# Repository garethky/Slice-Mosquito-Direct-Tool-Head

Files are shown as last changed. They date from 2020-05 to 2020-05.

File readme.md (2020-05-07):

# About

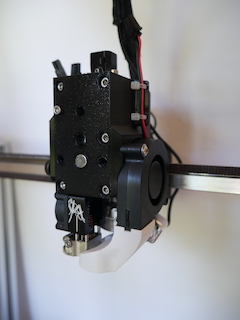
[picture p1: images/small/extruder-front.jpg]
Extruder Front

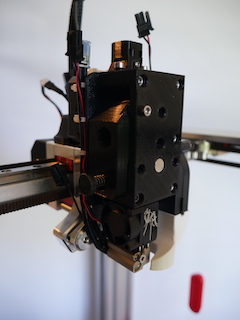
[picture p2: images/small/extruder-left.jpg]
Extruder Left


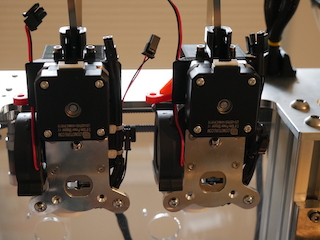
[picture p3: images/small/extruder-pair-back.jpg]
Extruder Pair Back

<a href="https://raw.githubusercontent.com/garethky/Slice-Mosquito-Direct-Tool-Head/master/images/extruder-pair-left.jpg">Extruder Pair Side</a>

This is a tool designed for the E3D Tool Changer platform. It uses the Bondtech Mini Gear (BMG) drive parts and the Slice Engineering Mosquito for a compact and light weight direct drive extruder.

# Source

The project was designed in OnShape and you can access the released design here: [E3D Tool Changer - Bondtech Mini Gear (BMG)/Slice Mosquito Tool Head](https://cad.onshape.com/documents/296b560eee7721bd4ef989d0/w/90142d42ff99dde68f53c17c/e/d21c095bd78c720c7f814c17). 

The project is configured to allow forking and export of .stl and other formats. Work may be in progress, for the latest tested .stl files please use this github repo.

STL files, this readme and these assembly instructions are maintained on [GitHub - Slice-Mosquito-Direct-Tool-Head](https://github.com/garethky/Slice-Mosquito-Direct-Tool-Head), you can also file an issue there.

## Why Build One?
* It's a geared direct drive extruder that can print faster and more precisely that the stock bowden tooling.
* The Mosquito hot end makes it very easy to swap nozzles without worrying about filament oozing out of your hot end. "Volcano" version of the Mosquito has the same nozzle hight so they can share wipers/brushes.
* It uses the stock dock pins in its stock location. No dock mods required.
* Light weight. Measured as 400g all up weight with tool plate.
* 5015 part cooling for quiet and powerful cooling.
* Compact size, wont steal space from other tools or collide with the printer frame.
* Designed for manufacture on FDM printers with no required support material in PETG filament.

## Project Status: Beta
Currently this project is in Beta. Now is a good time to print an extruder and try it out for yourself. Before this release, several prototypes were printed and tested to failure. Improvements to the design have been made that should overcome these issues. Numerous print-ability tweaks have been made to eliminate the need for support material when printing. Print-ability, usability and general fit/finish should be fine for general use. I'm installing printing 4 on my tool changer so I can work on multi-material and multi-color printing.

## Required Parts, Printing & Assembly
[Assembly Instructions](assembly-instructions.md)

## Extruder Setup and Printing
[Extruder Setup & Printing](setup.md)

# Related Work
This design contains modification of 2 parts provided by E3D: 

* [X-Carriage Cable Bracket](https://github.com/e3donline/ToolChanger/blob/master/STLs/X-Carriage%20Cable%20Bracket.stl)
* [V6 Cable Support](https://github.com/e3donline/ToolChanger/blob/master/V6%20Tool/STLs/V6%20Cable%20Support.stl)

The modifications are just to move the bolt holes to re-position the parts. The source for the changes is available in OnShape. Later versions will aim to remove these parts as they are not central to the design and really not ideal, but they work well enough for now. Thank you E3D for making the designs available under the GPL.

# Q and A

### Is this done, will there be changes?

Oh there are going to be changes... when I get time:
1. Prusa Labs has released their filament sensor as open source and inexpensive third party kits are available. This will enable automated filament loading and unloading and filament runout detection. The next major release will have the filament sensor integrated as an optional add-on.
2. I'm not satisfied with the way the filament enters the extruder. This release eliminated the push fit connector I was using. Bondtech's connector is inexpensive and is being evaluated. for now simply using no connector is fine and makes filament swaps easier.
3. The Cable Support that attaches the metal band and wiring loom is something I want improve and possible integrate into the motor plate. The extra part and fasteners dont seem to be beneficial. Cable routing in general isnt as clean as I wanted.

### Will you adapt this design for the E3D V6?

The V6 mounts differently and the extruder would have to be split along the filament path to capture the mount. Thats a very big change and it wont be easy to maintain both versions. There is also the [Hemera](https://e3d-online.com/e3d-hemera-175-kit) which is a great value vs this design. You're free to fork the design if you like.

### How about Duet 3 Tool Board support?

I like the concept but the boards are kind of large. My worry with this is mostly about hwere to put it without making the whole package larger.

### That Mosquito fan is a menace

I noticed that too. Slice recommends running their fan at 70% (per https://www.sliceengineering.com/pages/documentation). Only the main Duet 2 board has PWM controlled ports for the hot end coolers to permit this. The Duet 3 expansion board has PWM fan ports. I'm upgrading to the Duet 3 and I'll be evaluating the noise at the 70% setting with 4 extruders. If thats too noisy, a mod to run a quieter fan would be something to consider. To have any benefit we would have to go up to the 40mm Noctua fan.

### Will you post this to Thingiverse/Prusa Printers/Other Platform

For the time being no. The audiance for this pretty narrow right now and for my workflow github is just nicer.

# Happy Printing!

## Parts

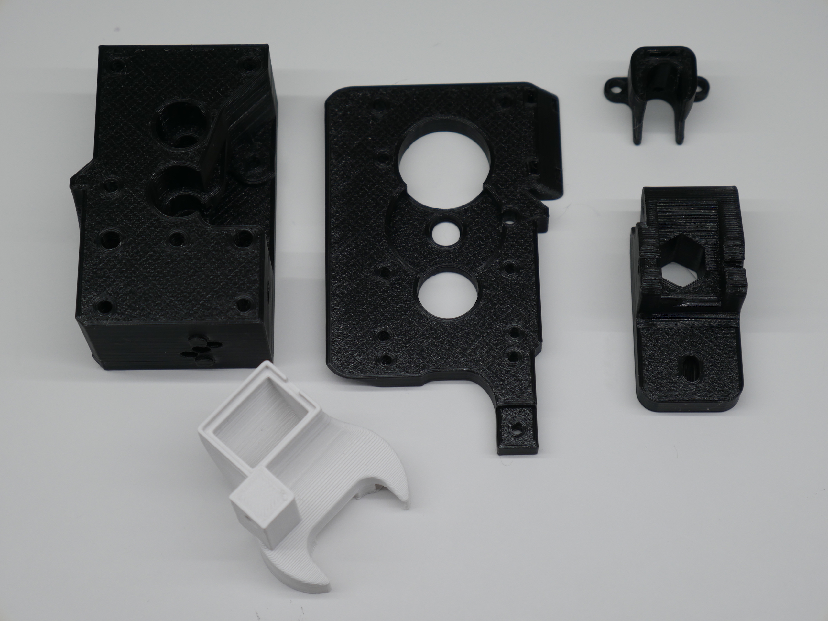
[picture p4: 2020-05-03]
images/assembly/printed-parts.jpg

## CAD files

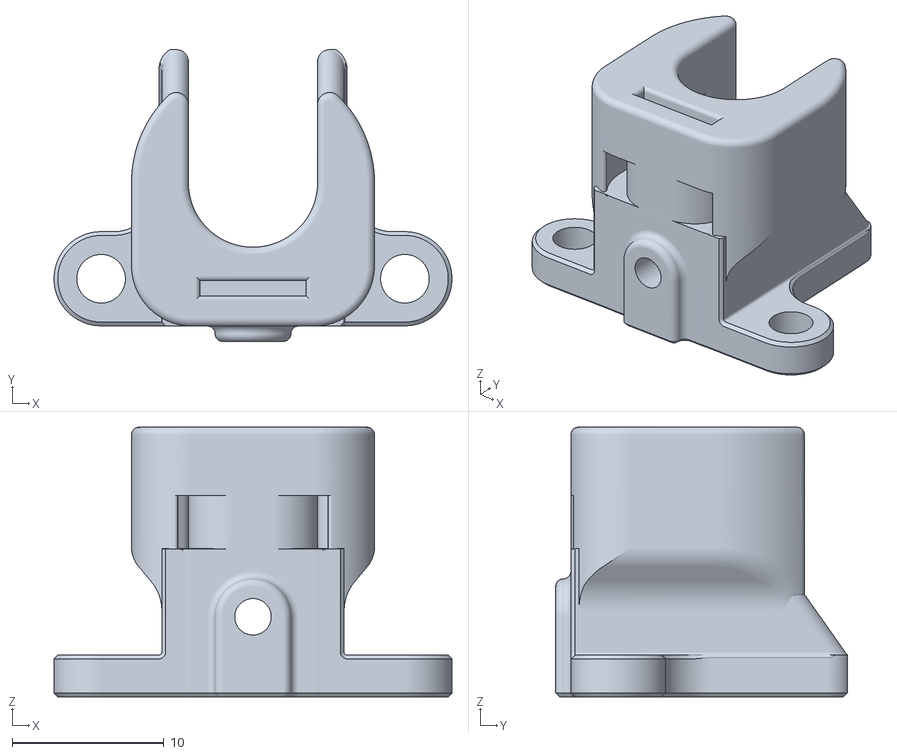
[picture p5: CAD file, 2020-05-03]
STL/Cable Support.stl
26.2 x 19.2 x 17.8

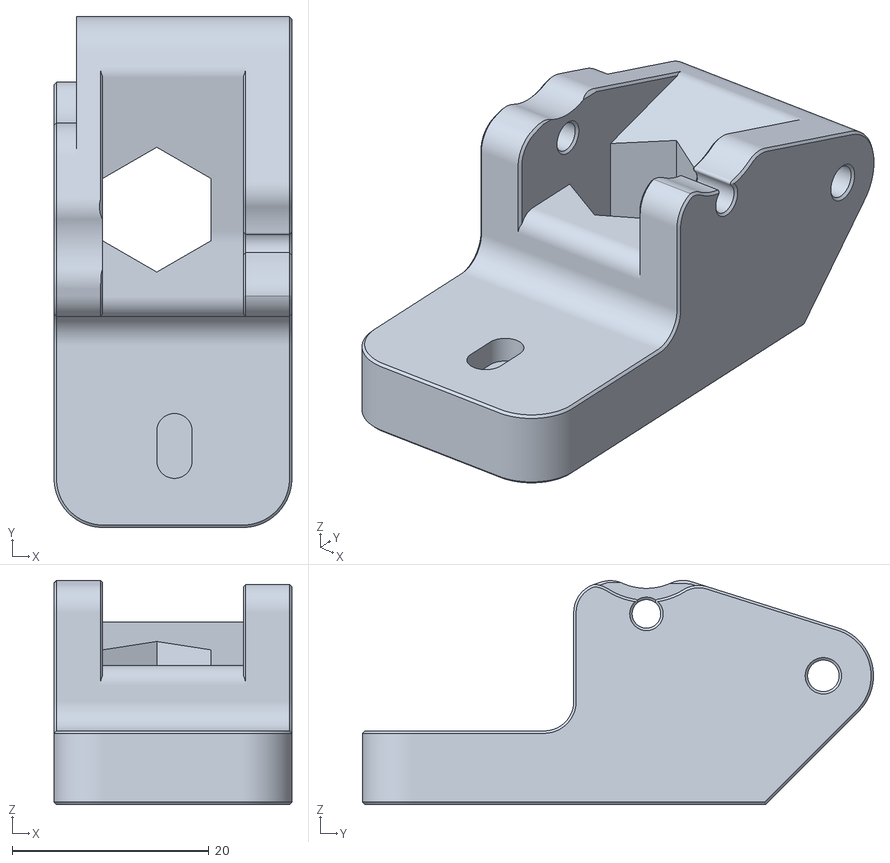
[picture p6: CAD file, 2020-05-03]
STL/Idler.stl
24.2 x 52.0 x 22.8

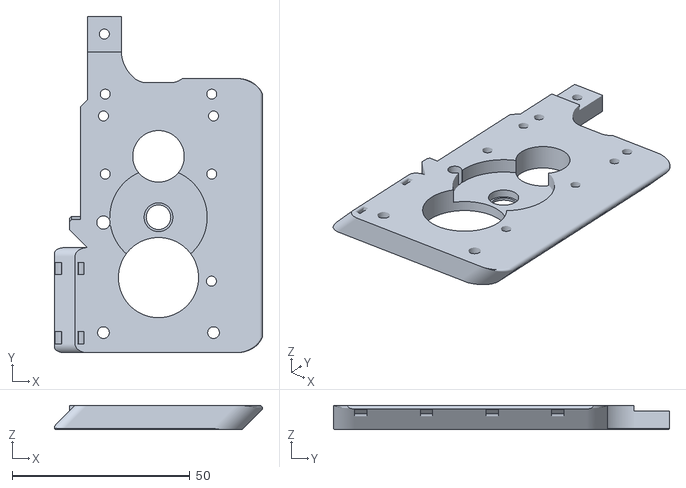
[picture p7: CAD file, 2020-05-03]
STL/Motor Plate.stl
58.6 x 94.7 x 6.79

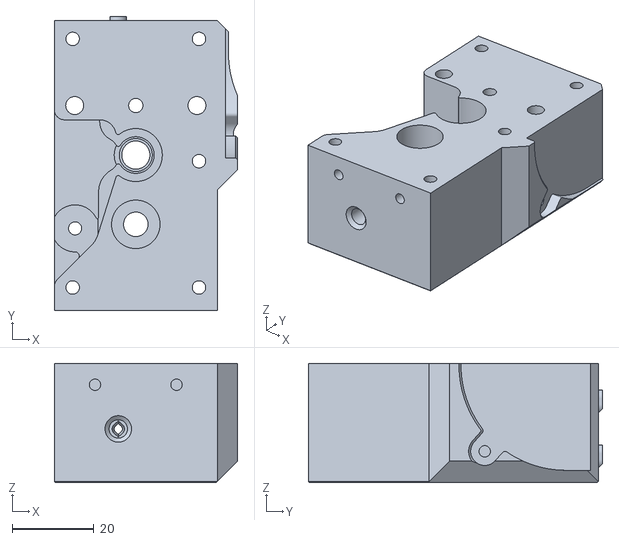
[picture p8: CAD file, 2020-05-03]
STL/Hot End Block.stl
45.0 x 72.1 x 29.2

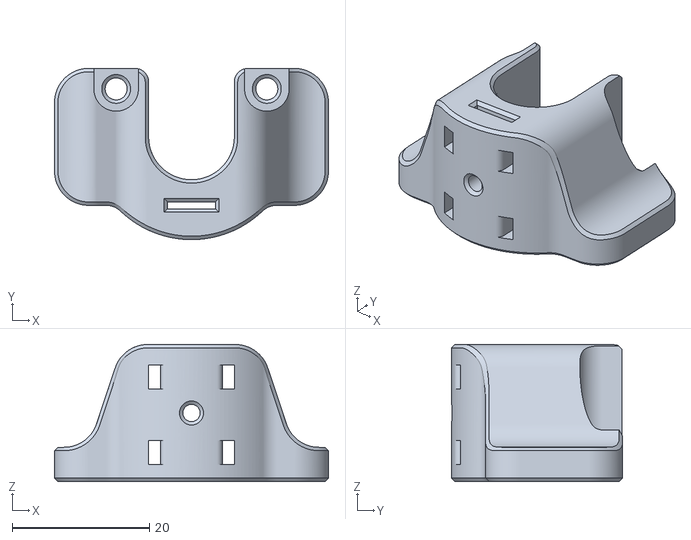
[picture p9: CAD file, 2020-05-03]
STL/X-Carriage Cable Bracket.stl
40.0 x 25.0 x 20.0

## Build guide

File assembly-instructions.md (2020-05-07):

## Hardware Required

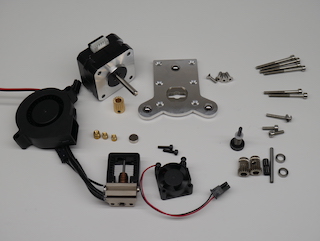
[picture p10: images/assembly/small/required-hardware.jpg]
all required hardware


* [Slice Mosquito Hot End](https://www.sliceengineering.com/collections/mosquito-the-professional-hotend). It does come with all the 2.5mm screws you will need to mount it. Note that the [cooling fan](https://www.sliceengineering.com/collections/accessories/products/fan-for-mosquito-hotend%E2%84%A2), [thermistor](https://www.sliceengineering.com/collections/accessories/products/thermistor-high-temperature) and [heater cartridge](https://www.sliceengineering.com/collections/accessories/products/50w-heater-cartridge) are not included and need to be purchased separately. E3D header cartridges and thermistors will work but the fan is particularly difficult to source so make sure your get that.
* Bondtech BMG Parts. They can be ordered as 'Spare Parts' directly from Bondtech (or from one of their local distributors like Filastruder) and wont cost as much as an entire BMG extruder:
    * 1 x [Bondtech Gear Kit 1.75/5.0](https://www.bondtech.se/en/product/drivegear-kits/) thats for 1.75mm filament and M5 shafts. The idler shaft included in the kit will no be used.
    * 1 x [Motor Gear](https://www.bondtech.se/en/product/motor-gear/)
    * 1 x [Reduction Shaft Assembly](https://www.bondtech.se/en/product/shaft-assembly/)
    * 1 x [3.0 x 32mm Shaft](https://www.bondtech.se/en/product/shafts/) You will need to cut this down to 24mm to be used as the idler shaft. This is the same size that Prusa use in their MK3 idler design. It's not a standard Bondtech part.
    * 2 x [5mm x 8mm x 2.5mm Bearings](https://www.bondtech.se/en/product/ballbearing-5x8x2-5/)
    * 1 x [Thumb Screw Assembly](https://www.bondtech.se/en/product-category/spare-parts/bondtech-spare-parts/thumbscrew-assembly/)
* A NEMA 17 stepper, preferably a "pancake" 25mm stepper, such as the [LDO-42STH25-1404MAC](https://www.bondtech.se/en/product/nema-17-motor-slim-power-ldo-42sth25-1404mac-0-9-degree/)
* Hardware 
    * M3 socket head cap screws:
        * 4 x 35mm
        * 2 x 30mm
        * 1 x 20mm with washer (a button head would also work)
        * 1 x 15mm
        * 2 x 10mm
    * 4 x M3 x 10mm Flat Head Cap Screws
    * 1 x M3 x 5mm set screw
    * Melt in Brass inserts for plastics
        * 2 x M2.5 x 5.5mm brass inserts, such as these: https://www.amazon.com/dp/B07NBPGTY2
        * 1 x M3 x 4mm brass threaded insert, such as these: https://www.amazon.com/dp/B077CJV3Z9
        * Note: dont cheap out on these parts as they are safety critical, [see testing by CNC Kitchen](https://www.youtube.com/watch?v=G-UF4tv3Hvc).
* Short length of PTFE tubing (~30mm)
* 8mm x 3mm Magnet (This size is [not uncommon](https://www.amazon.com/s?k=8mm+x+3mm+neodymium+magnets))
* 7+ small zip ties
* E3D ToolChanger [Tool Plate](https://e3d-online.com/toolchanger-blank-plate)
* A 5015 24V cooling fan such as [this one](https://www.amazon.com/dp/B07WFKPLWY).

## Printing The Parts

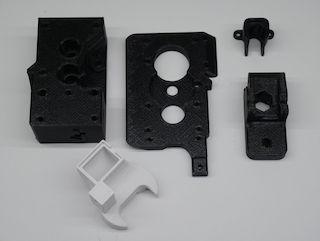
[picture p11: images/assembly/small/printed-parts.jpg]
all printed extruder parts


Every part has a face that was designed to print down on the print bed to help eliminate the need for supports. The SLT files should correctly orient the parts in your slicer when imported.

The extruder parts were designed to be printed in PETG. But the Fan Nozzle should only be printed in ASA, ABS or another hight temp filament.

I suggest using these settings for the extruder parts:
* 0.4mm nozzle
* 0.2mm layer height
* 3 perimeters (hot melt inserts need some material to melt into)
* 20% Gyroid or Grid infill

# Assembly
## Prepare the Stepper Motor

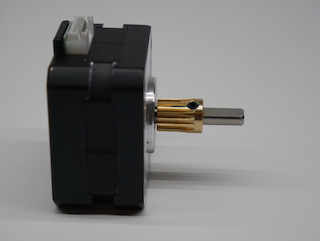
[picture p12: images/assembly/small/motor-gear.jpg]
motor gear


1. Install the drive gear on the stepper shaft so the toothed end faces the stepper and just clears the face of the stepper.

## Mosquito Preparation

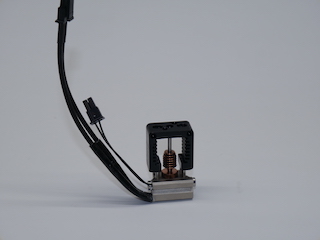
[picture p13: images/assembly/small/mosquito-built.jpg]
fully built mosquito


1. Install the heater and thermistor in the orientation shown. Follow Slice Engineerings instructions for doing this.

## Prepare the Hot End Block

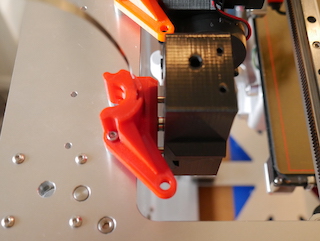
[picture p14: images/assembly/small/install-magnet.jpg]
install magnet


1. Install the magnet in the Hot End Block. It should be a press fit. Verify the magnet polarity with the Dock before installing. Use some thin CA glue to lock the magnet in permanently if desired. There is a hole in in the block that allows the magnet to be pushed out if polarity is wrong and for glue to get in.

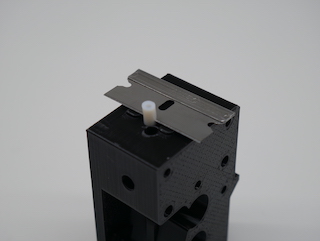
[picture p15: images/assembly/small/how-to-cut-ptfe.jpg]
how to cut ptfe


2. The extruder uses a very short length of PTFE tube to guide the filament into the Mosquito. The PTFE needs to be cut for length such that it fits into the 1mm deep pocket on top of the Mosquito, here is how to do that easily without measuring:
	1. Start with a longer length of PTFE tube thats easier to handle (30+mm).
	1. Cut one end square.
	1. Fully insert the square end of the PTFE tube into the bottom of the Hot End Block untill it stops (about 20mm).
	1. Cut the PTFE to final length by lining up a razor blade with the two locating bumps on the Hot End Block and cutting through the PTFE. The bumps stick out 1mm and act as a guide.

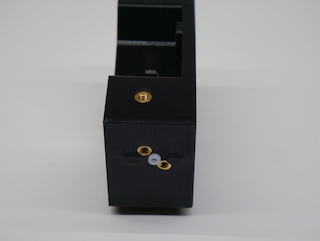
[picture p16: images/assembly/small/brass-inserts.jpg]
brass inserts installed


3. With the PTFE tube in place (this helps to prevent the thin walls from melting!), install the M2.5 brass threaded inserts for the Mosquito.
4. Install the M3 threaded insert for the Idler tension knob.

## Prepare the Idler

1. Cut away the printing support material in the tension knob hole/slot area with an exacto knife.
1. Place the Bontech idler gear with its two needle bearings into its final location in the idler. The hobbed section of the gear goes in front of the viewing window.

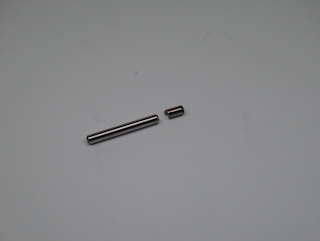
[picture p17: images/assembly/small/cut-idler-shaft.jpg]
cut idler shaft with cut off


3. Cut the 32mm x 3mm shaft down to 24mm.

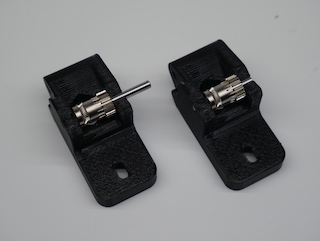
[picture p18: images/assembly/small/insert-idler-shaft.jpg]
insert idler shaft carefully


4. Insert the 24mm x 3mm shaft through the assembly so that it does not protrude from either side of the Idler. Reasonable force is required as these parts are an interference/pretensioned fit. The idler gear should now spin freely and have a tiny amount of play left to right. 

## Assemble the Drive Line

1. Install the bearings in the Motor Plate and Hot End Block. A pencil or pen is a good tool to push them in with.

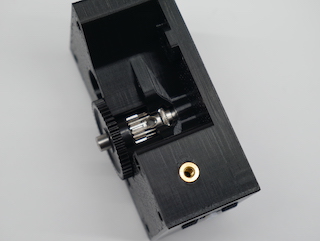
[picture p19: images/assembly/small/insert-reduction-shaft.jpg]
insert reduction shaft


2. Place the Bondtech drive gear onto the reduction shaft and install the assembly into the bearing you just placed in the Hot End Block.

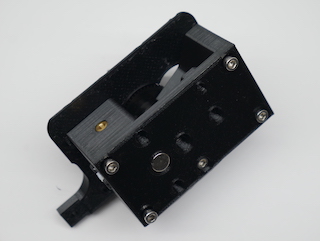
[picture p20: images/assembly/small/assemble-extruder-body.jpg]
/assemble extruder body


3. Mate bearing in the Motor Plate to the other end of the shaft.
4. Insert 3 of the 35mm screws into the location for the stepper motor to use as alignment guides. They pass through the Motor Plate.
5. Install 2 x 30mm bolts into the bottom of the hot end block. These thread into plastic in the Motor Plate. Start the threads but don't tighten yet.

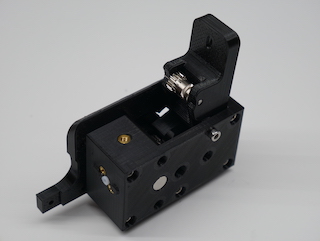
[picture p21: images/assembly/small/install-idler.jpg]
install idler


6. Install the idler with the last 35mm long screw as its pivot. Snug the idler screw but do not over tighten. The idler should swing freely on its pivot. If it doesn't swing freely, you might have a little over extrusion on the idler sides that can be sanded down.
7. Tighten the two 30mm screws at the bottom now.

## Aligning the Bondtech Gear Train

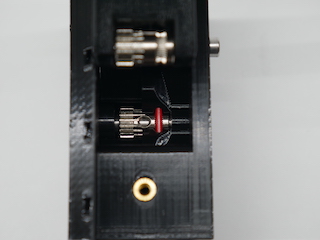
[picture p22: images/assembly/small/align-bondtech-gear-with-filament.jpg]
align bondtech gear using some filament


1. Insert a piece of filament through the extruder. It should pass though the hobbed section of the drive gear and hold it in place.
1. Now you can move the reduction shaft left and right while the drive gear stays in place. Try to center the large black plastic reduction gear between Motor Plate and the Hot End Block.
1. Tighten the set screw in the Bondtech drive gear to lock in this position.

You should get a free running gear train that does not rub on either of the printed parts when the filament is pulled through the extruder.

## Final Assembly

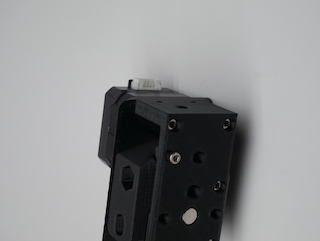
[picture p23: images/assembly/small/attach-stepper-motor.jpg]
attach stepper motor


1. Attach the stepper with the 3 x 35mm screws.

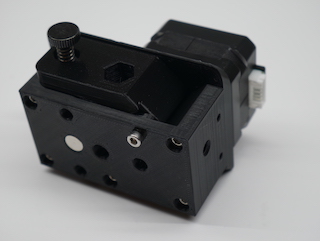
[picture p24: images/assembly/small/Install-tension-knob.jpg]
install the tension knob


2. Install the idler tension knob.
    1. Prusa says you only need enough tension to get the filament to feed and not slip. At this point you should still be able to insert filament by hand.

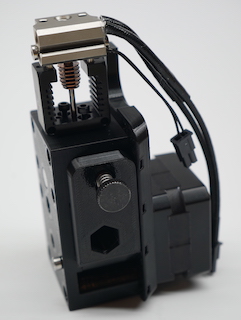
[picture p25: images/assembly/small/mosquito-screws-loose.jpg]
mosquito with screws before tightening

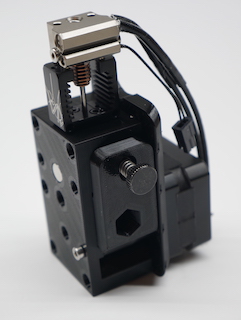
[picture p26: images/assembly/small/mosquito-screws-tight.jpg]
mosquito with screws fully tightened


3. Install the Mosquito onto the Hot End Block with the M2.5 x 10mm bolts included with the Mosquito kit (the longest ones). Make sure the heater cartridge/thermistor faces the idler side of the extruder.

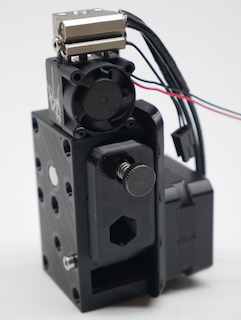
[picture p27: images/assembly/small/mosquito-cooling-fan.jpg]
mosquito cooling fan


4. Install the fan with its included button head screws and have its wires join up with the thermistor/heater wires.

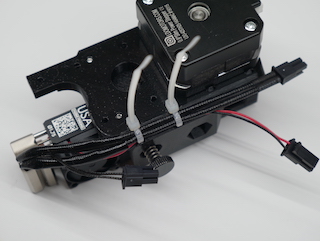
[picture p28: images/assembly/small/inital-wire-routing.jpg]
inital wire routing


5. Use 2 zip ties to hold the hater and fan wires to the wire guide as shown. You can route the thermistor wire in between the heater wires so it stays centered but don't zip tie it at this time.

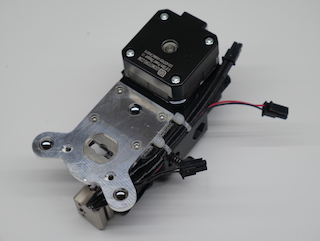
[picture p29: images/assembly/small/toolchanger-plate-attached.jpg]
toolchanger plate attached


5. Attach the E3D ToolChanger plate with the 4 M3 x 10mm screws

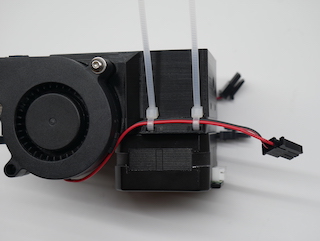
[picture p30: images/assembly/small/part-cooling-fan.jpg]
part cooling fan attached


7. Attach the 5015 fan with 1 M3 x 20mm screw with washer

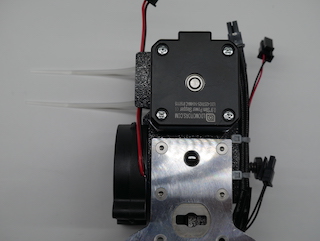
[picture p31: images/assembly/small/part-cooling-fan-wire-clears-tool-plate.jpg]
part cooling fan wire clears tool plate area


8. Use 2 zip ties to secure the 5015's fan wire to the wire guide. The wire should remain clear of the ToolChanger Tool Plate area.

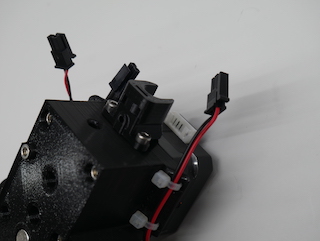
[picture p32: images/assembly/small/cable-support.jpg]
cable support


9. Attach the Cable Support with the 2 M3 x 10mm screws.
10. Install the M3 x 5mm set screw into the hole in the cable support.

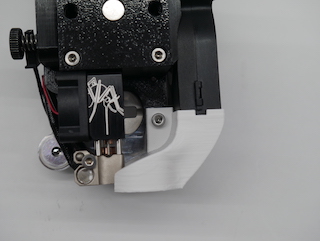
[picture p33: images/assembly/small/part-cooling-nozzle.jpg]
part cooling nozzle


11. Finally attach the part cooling nozzle with an M3 x 15mm screw. 

## Attaching The Tool
Connection are be made in the same way that the stock V6 tool. The umbilical cable needs to be modified to get a stepper drive cable to the extruder. This is not something that I'm going to try and cover here.

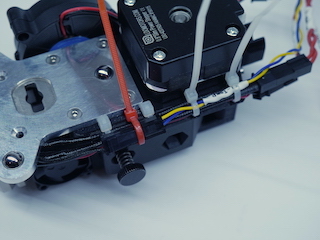
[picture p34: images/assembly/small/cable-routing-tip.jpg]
Cable rotuing of annoyingly short thermistor connector tip


One specific suggestion to keep things neat is to pass a zip tie (pictured in red) behind the thermistor wires  to clamp the thermistor connector in place.

<a href="https://raw.githubusercontent.com/garethky/Slice-Mosquito-Direct-Tool-Head/master/images/x-cable-mount.jpg">X-Carriage Cable Bracket Installation</a>

The stepper motor will collide with the stock X-Carriage Cable Bracket. An alternative part is included: (Modified X-Carriage Cable Bracket)[STL/X-Carriage Cable Bracket.stl]
This is a modification the stock E3D part and should be a drop in replacement. 

Next Step: [Extruder Setup and Tuning](setup.md)

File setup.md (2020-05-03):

# Extruder Setup and Tuning

## Duet Configuration

### Tool Clearance

This tool has a motor that sticks out over the tool changer head and interferes with the stock X-Carriage Cable Bracket. A remix of that part is included as a drop in replacement for the stock part.

### Slice Thermistor Setup with Duet

If using, the [RepRap Configurator](https://configtool.reprapfirmware.org/Heaters) has the settings you need, you can generate a config and pull the thermistor line out. Looks like this:

```
M305 S"T1" P1 T500000 B4723 C1.196220e-7 R4700 
```

### Tool Location Adjustments

This tool sticks out further from the dock than the stock V6 tool. You'll need to edit `tpreN.g` and `tfreeN.g` to change the location where the tool is collected. Please use the calibration procedure [outlined by E3D](https://e3d-online.dozuki.com/Guide/10+-+Commissioning./104?lang=en) to work out the correct offsets for your printer. Expect your Y offset to be something like `239` to `240`.

### Z Offset

You'll also need to tweak the Z offset in `config.g`. I ended up with an offset of about `4.1` with an E3D Nozzle X installed. Be careful and set the offsets correctly to avoid a crash.

## Printing & Slicing
I am by no means an expert in 3D printer tuning. One of the big learning experiences for me on this project was just how much these settings impact print quality. For many weeks I though I had a problem with the extruder design but it ended up being largely down badly selected Acceleration and Jerk values. Below is how I now think about tuning these parameters:

### Max E-Axis Acceleration

This needs to be high enough that your extruder can reach your desired retract speed for the majority of your retract length. Retracts are generally the most demanding speed changes on an extruder axis. You can use the calculator here to build an intuitive sense for how that works: https://blog.prusaprinters.org/calculator/#speed

Suggested value: **5000mm/s^2**

The default in Marlin is 10000K mm/s^2, double the above value, so I'm probably being conservative here.

Low extruder acceleration has several bad effects on print quality that you can see, including:
* Weak infill (extruder cannot accelerate fast enough)
* Over extrusion on solid layers (deceleration not fast enough leading to ooze)
* Lots of plastic clinging to the nozzle or extra plastic blobs on the part.
* Bad seams
If you are having these issues try raising the extruder acceleration.

### Max E-Axis Instantaneous Acceleration / Jerk

This is an exception to regular acceleration. If the change in speed required falls within this range the stepper will be commanded to do it instantly without breaking it up over multiple steps.

Values between 1mm/s and 5mm/s seem to be a good place to start. Duet takes this in mm/minute so we must multiply by 60:

Suggested value: **90mm/min** (i.e. 1.5mm/s)

Very high jerk values can cause unnecessary wear on the extruder. You can hear this as clicking/clunking of the extruder gear train as it snaps in the opposite direction on a retract or de-retraction. Conversely, if the value is too low printing will slow down when Pressure Advance is used. If you see slowing you will need to raise the Jerk value (and possibly acceleration) and re-tune pressure advance. A jerk value that sounds harsh without pressure advance may end up being too low with it on. For reference, Marlin defaults this to 300mm/min (5mm/s). If you find you need values much higher than this, raise the acceleration value instead.

### Expect to Print Hotter
You may need to raise the print temp by 5°C to 10°C over what you might have used with an E3D V6 tool. The most noticeable artifacts of low print temps is poor layer adhesion and gaps at seams.

I'm not sure if this is related to the cooling fan arrangement, the part cooling fan or the Mosquito's melt zone being shorter.

### Set Retractions to the Nozzle Diameter
Slice Engineering recommends using the nozzle diameter as the retraction amount. 0.4mm nozzle == 0.4mm retracts.

But what about oozy filaments like PETG? Try starting with just double the nozzle diameter. If you still get stringing try reducing retraction speeds to 25mm/s (Thats my PETG sweet spot). Too much retraction distance can tear the filament inside the melt zone and lead to bubbles. You will head a "popping" sounds when the bubble is extruded. If you get popping and voids in your prints, try reducing retract length.

### Pressure Advance Tuning
When you have dialed in all of the above variables its time to tune pressure advance with a test print. I like Marlin's [K-Factor test](https://marlinfw.org/tools/lin_advance/k-factor.html). You'll have to edit the .gcode for the Duet but its not hard once you have a slicer set up with custom GCode that you can copy from. A good range of values to test on this extruder is `0.01s` to `0.2s`in `0.01s` increments. You're value will depend on your print setting, speeds and the ooziness of your filament. My optimal number in PETG ended up being **0.09s**.

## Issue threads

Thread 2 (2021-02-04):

Tolerances for filament path should be widened a bit.

im000000, 2021-02-04:
I was having some difficulty getting my filament to feed through the opening into the hotend. I think the filament path should be widened a bit to allow for easy passage of filaments.

garethky, 2021-02-04:
I'm always looking for data to support changes like this. I have been benchmarking this design against the Prusa MK3S parts because they have so many users successfully printing and using them. I guess I never checked this particular dimension:

The filament path in the current design is set at 2.0mm. It's also has a "birds mouth" profile to combat any blockage due to bridging:
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

The Prusa design uses a value of 2.4mm for the filament path diameter:
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
see: [extruder-body.stl](https://github.com/prusa3d/Original-Prusa-i3/blob/MK3S/Printed-Parts/STL/extruder-body.stl)

So a bit is ~0.4mm 😁, this change will be in the next commit to the dev branch. I also added the same 0.6mm filet they have around the opening. The Prusa part don't have the "birds mouth" because the split line is down the middle of the filament path, meaning there is never a bridge. The birds mouth does give slightly more room for the filament to wriggle side-to-side vs a straight tube. I'm going to remove it from the bottom, since its technically unnecessary there. If we find there is a problem with flexibles we might try removing it from the top as well.

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

I'll put these changes into the dev branch when I make the next update.

im000000, 2021-02-05:
thx, I will grab your dev branch over weekend.

I am now printing with PC Poly Max filament.  Instead of Prusament PC .
 My current print doesnt show any warping at least on the bed.  using an
enclosure + skirt + brim to combat this.  Also using a filament enclosure
to keep the PC dry.

thx

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

garethky, 2021-02-05:
Just to be very clear: I haven't pushed this change to the development branch yet! I have a bunch of changes that I am doing in the OnShape file right now:
* Soft mounting the 5015 fan
* Totally re-designed part cooling nozzle (this is my third attempt)
* Fixes to the fan shroud to prevent warping
I need to print these changes myself and validate that the tool at least passes the heater tuning test before uploading them. If all goes well I should have something to post by Monday.

garethky, 2021-02-05:
And maybe I should open all 3 of those issues as bugs here to track whats being changed...

garethky, 2021-02-08:
I just pushed this change to development along with all the other work.

im000000, 2021-02-08:
Thx , I will look at it next week and let you know how it goes.

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

im000000, 2021-02-09:
Hi,

I have some design improvement suggestions , specifically with hot end
block and idler --   I printed the development branch version thinking i
could replace it with main branch -- since I dont have the new fan design
--  I couldnt test it immediately but my observations still hold.

I happen to have a Prusa MK3s printer and upgraded the hot end setup with
this design:  https://mihaidesigns.com/pitstop

My main reason for moving away from Prusa's design was that I like printing
with flexibles , specifically ninja tek and it was always a hassle to
untangle the hotend every time the filament jammed.

This comes back to your design, I think the tolerances should be relaxed to
accommodate something like flexibles.  I think a flexible friendly design
will  solve other issues along the way.

I see 2 issues:
1.-- The idler design does not allow it to squish the filament, if my gears
are just a little far away, there is no corrective way to adjust for this
--prusa's mk3 design allows a lot of room to adjust the closeness of the
gears in the idler.

2.-- The PTFE tube should be more like mihai's design.
https://mihaidesigns.com/pitstop  --- the minute the gears start feeding
the filament they should direct the filament straight into the ptfe tube.
    The current design feeds filament into a tunnel that has an obstruction
which is the  ptfe tube that is embedded inside the filament path.  Think
again of flexible filament being fed into this.  If it is fed too fast it
can jam and wont go into the ptfe tube easily.

That said, I am going to take a stab at tweaking your design, if you
dont mind.    I am using Blender for my 3D work.   When I have something I
will let you know.

Thx again for your efforts.

Irumbo

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

garethky, 2021-02-09:
The dev branch and mainline parts are not compatible. The idler had to be shortened to make room for the 40mm fan. If you are trying to mix parts that might cause an issue.

I don't understand issue #1? Are you saying that you can't get the idler closed enough? The idler gears mesh before the face of the idler makes contact with the extruder body. The actual design has the filament squished slightly with the idler still not touching the face of the extruder body:

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

For #2, this design is pretty standard now. Just looking around, both the newest version of the [Prusa MK3S extruder](https://github.com/prusa3d/Original-Prusa-i3/blob/MK3S/Printed-Parts/STL/extruder-body.stl) and the [Voron Afterburner extruder](https://github.com/VoronDesign/Voron-Afterburner/blob/master/STLs/Gantry/Direct_Feed/extruder_body.stl) use this same concept. Printing the complex geometry is more reliable and provides tighter tolerances than cutting the PTFE without a jig did.

It is possible to configure parts in OnShape to have optional features, so I could have 2 versions of the extruder block, one with the feature and one with a plain hole, if you really want to cut the PTFE to shape.

garethky, 2021-02-09:
Might be worth looking at: [Filament path is not straight through Bondtech wheels](https://github.com/prusa3d/Original-Prusa-i3/issues/51)

im000000, 2021-02-09:
The idler is closing ok but design limits how close gears get together,  in
my case the filament is not being pulled through. But I can see the marks
it is making on filament.  It is also possible that the gear teeth are not
aligned properly vsomething I will verify.

I would have wanted in this design to be able to have the gears touch
together.

Prusa's design doesn't have any plastic preventing gears from getting any
closer.

I think freedom to be able to have gears touch should be a top
consideration.

In case #2 -- It was very hard for me to push the PTFE tube inside, so very
possible it didn't go in all way.

I would like to see the PTFE tube protruding a little when I open idler
door,  which will be tricky to get right because of tolerances.

I will be able to tweak the designs , have had some experiences doing that
with other designs to fit my needs.

Might use on shape as u suggest for now trying to become proficient with
blender since it is open source but may switch at some point.

It is very likely all this might be because of material I am using -- PC
but I think it is right material for this role

The again.

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

im000000, 2021-02-10:
I looked at the stl file for the hotend block and the measurements look
ok, with an eye to tweaking it.   Specifically the bottom part where the
ptfe tube fits.

I am going to use a smaller nozzle (2.5mm) to re-print the heater block and
see if the smaller nozzle will be a little more within spec for the
filament path.

If that doesnt work I will try and print the heater block in a vertical
position .

The main culprit I think now is the PC Max filament,  it generally prints
well and doesnt warp -- but every now and then you will see artifacts in
print where it oozes perhaps a little bit more filament than expected.
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
garethky, 2021-02-12:
In the above linked Prusa issue they note that the "ideal" designed gap between the bondtech gears is 8.7mm. I based the gap in this design on measurements taken from a BMG extruder. I got 8.6mm. The filament path is straight relative to that spacing:
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

I'm going to call that "good enough".

garethky, 2021-02-12:
This is an interference projection with +2 degrees of closure on the idler beyond what is possible now. I'll see what I can do to make this work for tighter grip on flexibles.
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

im000000, 2021-02-12:
Don't be in a hurry to do that yet.

I re-printed the hotend block using 2.5mm nozzle and it fixed the tolerance
issue I was having with the filament path.  I also widened the ptfe tube
path that connects to mosquito by a very very tiny amount but in retrospect
i don't think that was necessary.

The result of 2.5mm nozzle  is that the ptfe tube is able to easily slide
all the way into the area created to connect it to the mosquito hot end.
This is actually good for flexibles because the ptfe tube is now occupying
the whole space and reducing  chance of flexible jamming once it gets past
the gears.

Going forward I am going to use 2.5 mm nozzle for prints that require  very
tight  tolerances.

I am now looking into why my filament is not being picked up easily, when I
start extruding.  I think this could be loose gears not being tightened.

Will know some more after some more investigation and tweaking

Once I have filament feeding without much fuss, I will have a better
opinion to make.

In general flexibles might be a tough act to solve because of the limits
you have to work with concerning  the tool changer.

Thx again.

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

im000000, 2021-02-14:
Hi,

I fixed the issue with one of my tools not picking filament up.   The gear
assembly that connects to the stepper motor was loose so I tightened it up.

I think you have a very good design in your hands.    However it was not
picking up  flexibles,  I think the fix for this is to allow the idler
mechanism to be able to get much closer and get a firm grip on the filament.

I am going to tweak the heater block as well to make room for the idler
gears to grind against the filament.

The design you suggested is a good start, it will also require removing
some of the material on the rotating gear assembly so it doesnt prevent the
idler gears from connecting fully.

thx

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

garethky, 2021-02-14:
Here you go: [Add 2 degrees of clearance to idler ](https://github.com/garethky/Slice-Mosquito-Direct-Tool-Head/commit/0b50e7e5d4a089c8dc81de069408ee751e804964 )

I don't actually think this is going to do anything for your issue though. But you can try it with the drive gear not in place and see that it closes more. Its just that the gears are fully meshed and can't close anymore. The cylinders of the Bondtech gears never touch at maximum closure (if they did we would have problems hitting the set screw!).

I tried hand feeding some TPU through an extruder (turning the reduction gear by hand so I could feel what was going on) and I didn't have a problem. You can apply a LOT of tension with this design. Its because of the leaver arm design and short spring, see [issue 6](https://github.com/garethky/Slice-Mosquito-Direct-Tool-Head/issues/6)

im000000, 2021-02-14:
Thx will try it out next after I have tested my modification.

I was also able to feed in tpu by hand with idler closed but without
stepper motor , attached and it seemed to feed in ok on original design — I
am using ninjaflex by the way which is very soft.

My guess is once the stepper motor is added it realigns everything by a
little bit.

btw Prusa doesn’t include a profile for ninja flex in their slicer filament
profile.

What I have done in my tweak is extend the length of idler by about .7 mm
around the area where the two gears meet and also remove area that would be
occupied by gear on idler  from hotend block.

If it works I will let you know.  This is what hotend block looks like (
see attachment )

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

im000000, 2021-02-14:
I will test your design change it is similar to what I had in mind after
looking at it.  It will take me about a week or so before I can give you an
update.   I am going to order the fans that work with this.  I might also
apply your design change to the older version also.

thx

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

garethky, 2021-02-15:
The idler should be all you need to print. Thank you for testing!

- Gareth

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

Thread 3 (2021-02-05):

Part cooling fan blows on the hot block, causes clogging

garethky, 2021-02-05:
The part cooling fan, currently in mainline, blows onto the hot block of the mosquito an causes a large temperature differential in the block. A heater tune in RRF with the part cooling fan at 100% will fail as the heater cannot keep the block hot. Its also possible to get filament clogging if the part cooling fan is used at too high of a setting.

A temporary part cooling fan is currently checked into the dev branch to alleviate this issue but its part cooling performance is far from optimized.

Some problems with the design:
* The selected height for the floor of the nozzle is too high
* The openings in the nozzle are too tall, allowing air to flow directly into the hot block.
* There is unequal air distribution between the center vent and the side vents, the center vent passes the majority of the air.

garethky, 2021-02-15:
The latest nozzle design has been performing well, printing nice test parts in PETG and PLA. I also don't have any issues tuning the heater with the fan running at 100%.

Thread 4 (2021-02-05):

5015 fan makes a loud noise during some moves

garethky, 2021-02-05:
The Sunon "Vapo-Brearing" fans that I am using float on their shafts, unlike ball bearing fans that are locked to the shaft by the bearings. If the fan gets excited by resonance in the motion system it can vibrate and amplify this noise, causing a loud screech.

One possible solution is to use silicone vibration isolation mounts. Luckily we get 4 of these in the package with the Noctua 40mm cooling fan so this would not be an extra cost to the builder. This requires space to be mounted so the fan will have to be moved away from the extruder body.

For builders that want to use a ball bearing fan there should be an option for hard mounting the fan. This requires 2 parts in the build.

garethky, 2021-02-08:
Comited a "Soft Mount" bracket that allows the 5015 to be mounted.

One unhandled problem is what to do with the narrow "ends" of the soft mounts. They can be cut off but that makes it hard to use them more than once. They can be stuffed under the fan but its not really secure. Some kind of bracket is needed to retain them out of the way.

garethky, 2021-02-10:
Noise is improves but not eliminated. The fan is still coupled to the cooling nozzle which is directly coupled to the frame. Running tests with no nozzle shows that the noise in almost completely eliminated. The speed where it is worst on my machine (with 0.9 degree motors) is 55mm/sec. This is a pretty common speed for some slower print moves.

Next step here is to investigate isolating the fan from the part cooler. Maybe with some of the same material that is already isolating the fan, as that would keep the parts list short.

garethky, 2021-02-11:
I've been doing a separate deep dive investigation into using StealthChop on the ToolChanger. My ToolChanger was not correctly executing the requires auto calibration procedure to optimize StealthChop. The [calibration procedure](https://github.com/garethky/E3D-ToolChanger-Configuration/blob/master/duet-config/sys/stealthchop.g) now runs as part of my [homeall.g](https://github.com/garethky/E3D-ToolChanger-Configuration/blob/master/duet-config/sys/homeall.g#L17) and the result is an incredibly quiet and smooth machine. As a result I no longer have any noise due to the fan.

If someone is running in Spread Cycle mode and wants to argue for further improvements in this area feel free to open the issue back up.

Closed 2021-02-11.

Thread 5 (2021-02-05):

40mm fan duct is warping

garethky, 2021-02-05:
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

Tests of the 40mm hot end fan duct have shown that it warps or twists upwards over time. Some likely causes of this issue:

* There is not enough plastic around the screws to resist warping
* The shroud overall is not very thick or rigid

Adding more material around the mounting bolts would disturb the airflow further. One alternative is flipping the fan mounting such that the bolts go into it from the back of the mosquito. We can use some 2.5mm melt in inserts in the duct.

Switching to a loft for hollowing out the duct would also allow for an 'S' curve shape providing more plastic around the mounting points

Finally removing some material from the extruder back plate would allow the duct to be fully symetrical, allow it to have thicker sides and allow it to print without supports.

garethky, 2021-02-12:
This looks to be resolved based on testing with the new parts in the dev branch.

Closed 2021-02-12.

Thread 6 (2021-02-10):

Investigate over tension and filament grinding

garethky, 2021-02-10:
The current tension mechanism is easy to over tighten. This is in contrast to the MK3S and has a few causes:

1. The leaver arm on the idler is longer, requiring less torque for the same force applied to the filament
2. The Bondtech spring is shorter and stiffer, requiring fewer turns to apply the same force as the Prusa design.

The result is a very narrow difference between "just enough tension" and a loose screw. Unfortunately directly copying the Prusa design is not possible because the part cooling fan would block access to the spot where the tension bolt would go through the extruder. Another difficulty is finding a reliable source of longer springs.

Opening this issue to track ideas for a solution.

garethky, 2021-02-15:
I've tried with the Prusa spring and it gives a wider adjustment ranger. For this revision I think we should give links to both parts and discuss the tradeoffs.

More extensive changes may have to wait for a future design.

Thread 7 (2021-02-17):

here are images showing the revised idler being obstructed.

im000000, 2021-02-17:
[
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

](url)

garethky, 2021-02-18:
It looks like you are missing the bearing that supports the end of the shaft and stops it from deflecting away from the filament. Without that you can totally push the drive gear back and bottom out the idler. That would explain the issue you are having:

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

im000000, 2021-02-18:
Thx for catching this.  It is very easy to overlook

garethky, 2021-02-18:
I will take this as feedback to include a more detailed image of this step in the instructions.

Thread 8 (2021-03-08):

Possible re-design of the filament path opening past gears

im000000, 2021-03-08:
The V-Shaped design of the filament path opening when it gets past the gears might need a re-design to a more flat surface.

I got a jam when some pla filament got jammed then bunched up when getting thru.

I think what happened is that the filament might have come in at an angle -- not straight down vertical and part of the opening might have scraped off part of filament to cause it to bulge and then become unable to pass thru the hole.

a flat surface might not have sheared off parts of filament -- just a hypothesis.

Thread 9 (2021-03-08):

ptfe tube helper to cut out to exact length

im000000, 2021-03-08:
a cutout guide , should be included where user puts in ptfe tube and cuts off at either end.

if printed block  doesnt come out right, user will know almost immediately if they are unable to fit the ptfe tube fully.

my ptfe tube was cut a little bit short causing filament to seep under the extra space.  a precise cutout aid would have corrected for this. -- this is not a show stopper -- more a nice to have ..

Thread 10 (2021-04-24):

dev branch fan shroud a bit too wide

im000000, 2021-04-24:
the fan shroud in dev branch that attaches to heat sink should be slimmed down so it fits the dimensions of the heat sink at point of contact.

I am using slice engineering heater cables and they are a tight fit for cable routing

garethky, 2021-04-25:
Its a tight fit but it does work. The parts thickness was actually increased to combat warping due to heat creep, see: https://github.com/garethky/Slice-Mosquito-Direct-Tool-Head/issues/5

im000000, 2021-04-27:
What material did you use for the fan shroud?  I have printed mine in PC/PBT will likely switch to PC .. I modified design to shave a few mm.  If I used PC or ABS, I will revert back to your design.  Thx

im000000, 2021-04-27:
meant to say if you are using PC or ABS then I will revert back to your design.
I had a heat creep issue on my prusa printer and it was using a mix of PC and PETG parts on an E3D V6 Hot end. I was printing using PC filament when it happened.    The PETG part that was holding the V6 Hotend was deformed but the PC parts around it did not have the same issue.

garethky, 2021-04-27:
I printed my parts form Prusament PC blend. Its one of the reasons I think I may abandon this general design. Part cooling and hot end cooling need a lot more space and the general sideways orientation of the design doesn't provide for that. Also we now have a lot of small/lite extruder choices. So the value for Tool Changer users is in the aero design which is actually the weak point of this extruder design.

im000000, 2021-04-28:
I think the design is good.  The aero is nice and small but that is it's only advantage because of the heat creep issues that has plagued it.   All about trade offs.

I have been using the master version but will switch to dev branch but stay with stock slice fan.
The quality of the prints vs my prusa is much much better on the tool changer , I think the dev version for part cooling may be good enough.

Thx

im000000, 2021-09-13:
Hi,

I am working on an a extruder design based off of voron-0 for toolchanger ,
it is still very rough but nearly ready for testing.  I am using blender
which is not ideal for this by the way, if u want to look at it let me know.

switching to the dual 30x30 fan that the afterburner voron uses

the voron 0 project is here:
https://github.com/VoronDesign/Voron-0/tree/Voron0.1/STLs/Toolheads/Mini_Afterburner

thx

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

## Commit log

2020-01-05 Add STL Files
    Add STL files for inital release
    [Dock Receiver.stl, Fan Mount.stl, Fan Shroud.stl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]
2020-05-03 Merge R2 from Development (#1)
    R2 is a complete redesign. The "Tall" extruder layout has been adopted where the stepper overhands the X-Carriage. This version is a huge improvement in quality, robustness and simplicity of the design. Both print quality and durability have been tested and verified with many Kg of filament.
    [Cable Support.stl, Dock Receiver.stl, Fan Mount.stl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]
2020-05-03 Switch big im age URLs to link directly to the CDN
